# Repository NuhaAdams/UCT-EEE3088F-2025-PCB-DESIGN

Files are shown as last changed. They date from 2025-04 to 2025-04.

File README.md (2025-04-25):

# UCT-EEE3088F-2025-PCB-DESIGN
EEE3088F-MicroMouse Power Subsystem-Group55
# Overall Project
This repository contains the design files, documentation, and supporting resources for the Power Subsystem of the EEE3088F Micro-Mouse course project.
The project involved designing a power board for a micro-mouse maze-solving robot, while the sensing board, processor and motherboard were given.
# The Power Board
The power subsystem is responsible for:
Bidirectional control of 4 motors via H-Bridge drivers (DRV8833PWR).
5V and 3.3V regulated outputs using MC33063AD and TPS62200DBV regulators respectively.
Battery monitoring via INA219 current sensor on the I2C bus.
Battery charging from a USB-C 9V input, with two selectable charging modes (200mA and ~600mA).
High-side switching for two external 5V loads.
System ON/OFF control ensuring <30µA in the OFF state.
The PCB design meets strict budget and dimension constraints, fully interfacing with the Micro-Mouse motherboard.
# How this GitHub repo works
This GitHub repository serves as a central hub for all files related to the power subsystem design of the EEE3088F micro-mouse project.
Each folder in the repository is organized by function. Each of these folders contain the relevant documents that are associated with the design of the power subsystem.

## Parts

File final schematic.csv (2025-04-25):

Reference | Qty | Value | Footprint | LCSC
C1,C6 | 2 | 2.2u | Capacitor_SMD:C_0603_1608Metric_Pad1.08x0.95mm_HandSolder | C12530
C2,C4 | 2 | 0.01u | Capacitor_SMD:C_0805_2012Metric_Pad1.18x1.45mm_HandSolder | C1710
C3,C5 | 2 | 10u | Capacitor_SMD:C_1206_3216Metric_Pad1.33x1.80mm_HandSolder | C7171,C7171
C7,C20,C21 | 3 | 4.7u | Capacitor_SMD:C_0603_1608Metric_Pad1.08x0.95mm_HandSolder | C19666
C8 | 1 | 30p | Capacitor_SMD:C_0603_1608Metric_Pad1.08x0.95mm_HandSolder | C1658
C9 | 1 | 220p | Capacitor_SMD:C_0805_2012Metric | C107145
C10,C14,C16 | 3 | 10u | Capacitor_SMD:C_1210_3225Metric_Pad1.33x2.70mm_HandSolder | C13585,C13585
C11 | 1 | 100u | Capacitor_SMD:C_1210_3225Metric_Pad1.33x2.70mm_HandSolder | C15008
C12 | 1 | 1n | Capacitor_SMD:C_0805_2012Metric | C46653
C13 | 1 | 330u | Capacitor_SMD:CP_Elec_6.3x7.7 | C58277
C15,C17 | 2 | 150u | Capacitor_SMD:CP_Elec_8x10.5 | C38513
C22 | 1 | 0.47u | Capacitor_SMD:C_0603_1608Metric_Pad1.08x0.95mm_HandSolder | C1623
C23,C24 | 2 | 1u | Capacitor_SMD:C_0402_1005Metric_Pad0.74x0.62mm_HandSolder | C52923
C25 | 1 | 4.7u | Capacitor_SMD:C_0504_1310Metric_Pad0.83x1.28mm_HandSolder | C19666
D1 | 1 | 1N5819 | Diode_SMD:D_SMA | C2481
D2,D5 | 2 | LED | LED_SMD:LED_0603_1608Metric | C2286
D6,D7 | 2 | ~ | Diode_SMD:D_SMA-SMB_Universal_Handsoldering | C2481
J1 | 1 | Conn_02x16_Odd_Even | Connector_PinHeader_2.54mm:PinHeader_2x16_P2.54mm_Vertical
J3 | 1 | Conn_01x02 | Connector_JST:JST_PH_S2B-PH-K_1x02_P2.00mm_Horizontal
L1 | 1 | 10u | Inductor_SMD:L_0805_2012Metric_Pad1.15x1.40mm_HandSolder | C1046
L2 | 1 | 100u | Resistor_THT:R_Axial_DIN0411_L9.9mm_D3.6mm_P7.62mm_Vertical | C2931837
Q1 | 1 | 2N7002 | Package_TO_SOT_SMD:SOT-23 | C8545
R1 | 1 | 1 | Resistor_SMD:R_2010_5025Metric_Pad1.40x2.65mm_HandSolder | C2075154
R2 | 1 | 0.4 | Resistor_SMD:R_2010_5025Metric_Pad1.40x2.65mm_HandSolder | C912792
R3,R4 | 2 | 1.8k | Resistor_SMD:R_0603_1608Metric | C4177,C4177
R5 | 1 | 12k | Resistor_SMD:R_0805_2012Metric_Pad1.20x1.40mm_HandSolder | C22790
R6 | 1 | 0.1 | Resistor_SMD:R_2512_6332Metric_Pad1.40x3.35mm_HandSolder | C25334
R7 | 1 | 6k | Resistor_SMD:R_0805_2012Metric_Pad1.20x1.40mm_HandSolder | C2828725
R8 | 1 | 180 | Resistor_SMD:R_0805_2012Metric_Pad1.20x1.40mm_HandSolder | C22828
R9,R13,TH1 | 3 | 10k | Resistor_SMD:R_0603_1608Metric | C25804,C43113
R10 | 1 | 10k | Resistor_SMD:R_0805_2012Metric_Pad1.20x1.40mm_HandSolder | C25804
R11 | 1 | 30k | Resistor_SMD:R_0805_2012Metric_Pad1.20x1.40mm_HandSolder | C2907025
R12,R14 | 2 | 25k | Resistor_SMD:R_0603_1608Metric | C2828637
R16 | 1 | 6.8K | Resistor_SMD:R_0603_1608Metric_Pad0.98x0.95mm_HandSolder | C23212
R17 | 1 | 1.18K | Resistor_SMD:R_0805_2012Metric_Pad1.20x1.40mm_HandSolder | C17374
R18 | 1 | 1M | Resistor_SMD:R_0603_1608Metric_Pad0.98x0.95mm_HandSolder | C22935
R25,R26 | 2 | 1.13K | Resistor_SMD:R_1210_3225Metric_Pad1.30x2.65mm_HandSolder | C5204018
R27 | 1 | 1.5k | Resistor_SMD:R_1210_3225Metric_Pad1.30x2.65mm_HandSolder | C4310
R28 | 1 | 2.9k | Resistor_SMD:R_0805_2012Metric_Pad1.20x1.40mm_HandSolder | C4211
Rsc1 | 1 | 0.2 | Resistor_SMD:R_2512_6332Metric | C459674
TP1,TP2,TP3,TP4,TP5,TP6,TP7,TP8,TP9,TP10,TP11 | 11 | TestPoint | TestPoint:TestPoint_Pad_D2.0mm
U1,U2 | 2 | DRV8833PW | Package_SO:TSSOP-16_4.4x5mm_P0.65mm | C50506
U3 | 1 | INA219AxD | Package_SO:SOIC-8_3.9x4.9mm_P1.27mm | C87469
U4,U6 | 2 | TPS2553DBVR | PCBLIB_SOT-23-6_L2.9-W1.6-P0.95-LS2.8-BR_2025-03-28:SOT-23-6_L2.9-W1.6-P0.95-LS2.8-BR | C55266
U5 | 1 | TPS62200DBV | Package_TO_SOT_SMD:SOT-23-5 | C9048
U8 | 1 | MC33063AD | Package_SO:SOIC-8_3.9x4.9mm_P1.27mm | C127837
U9 | 1 | HX SS12D10G6 | PCBLIB_SW-TH_3P-P4.80-HX-SS12D10G4_2025-03-27 (1):SW-TH_3P-P4.80-HX-SS12D10G4 | C19189121
U10 | 1 | CH224K | Package_SO:SSOP-10-1EP_3.9x4.9mm_P1mm_EP2.1x3.3mm
U11 | 1 | BQ24075RGT | Package_DFN_QFN:VQFN-16-1EP_3x3mm_P0.5mm_EP1.6x1.6mm | C15464
USB1 | 1 | TYPE-C 6P LCH10.0 | PCBLIB_USB-TH_TYPE-C-6P-LCH10.0_2025-03-28:USB-TH_TYPE-C-6P-LCH10.0 | C5187470

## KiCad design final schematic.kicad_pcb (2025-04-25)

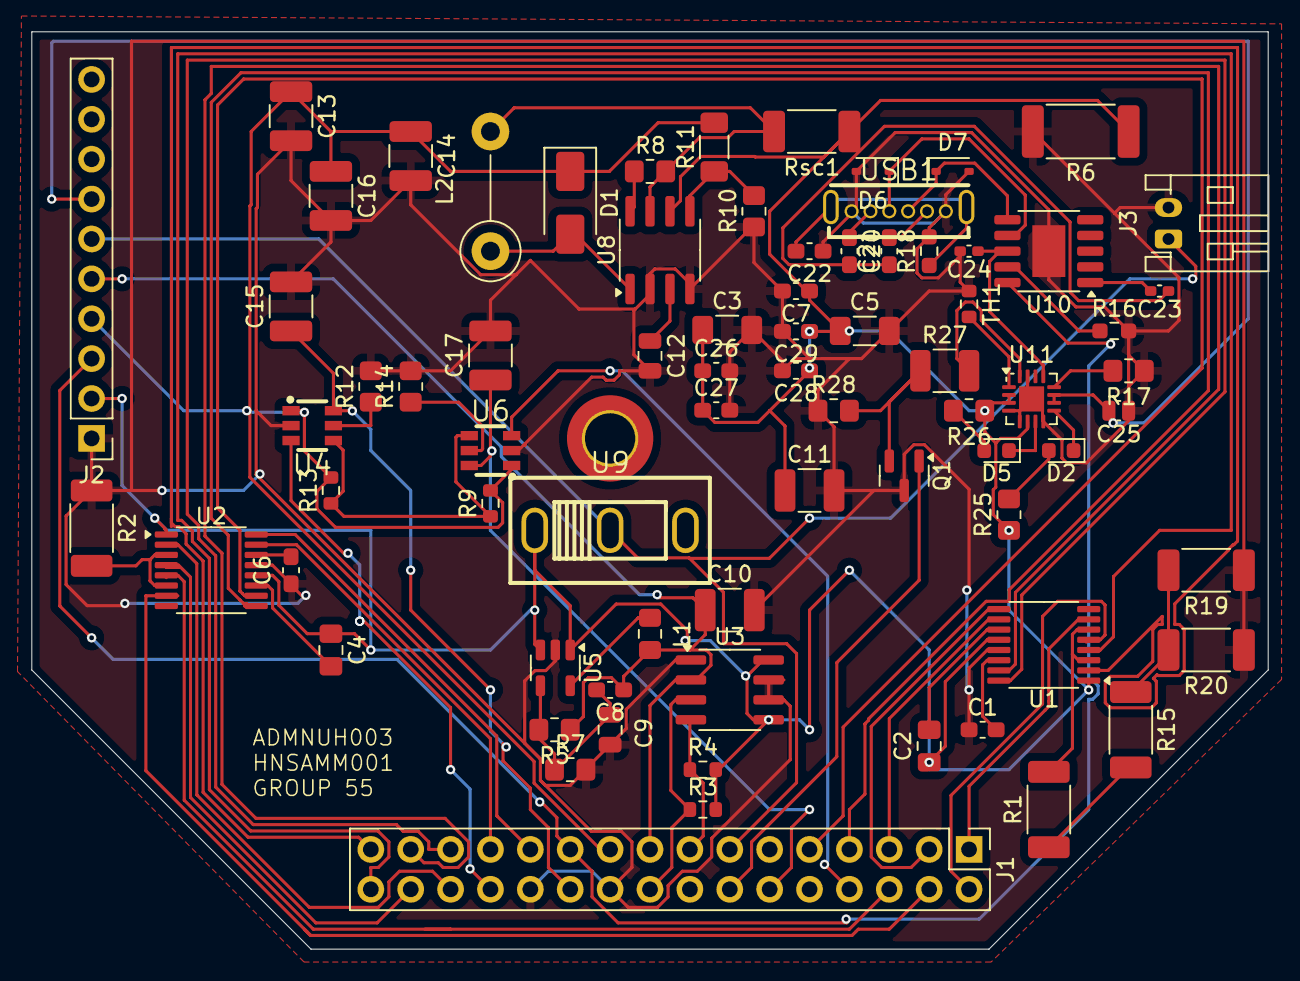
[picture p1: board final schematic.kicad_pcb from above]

Board: 2 copper layers, 78.7 x 58.4 mm, 75 parts (0 on the bottom side), 65 nets.

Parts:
C1, C6: 2.2u; C_0603_1608Metric_Pad1.08x0.95mm_HandSolder
C2, C4: 0.01u; C_0805_2012Metric_Pad1.18x1.45mm_HandSolder
C3, C5: 10u; C_1206_3216Metric_Pad1.33x1.80mm_HandSolder
C7, C20, C21, C26, C27, C28, C29: 4.7u; C_0603_1608Metric_Pad1.08x0.95mm_HandSolder
C8: 30p; C_0603_1608Metric_Pad1.08x0.95mm_HandSolder
C9: 220p; C_0805_2012Metric
C10, C14, C16: 10u; C_1210_3225Metric_Pad1.33x2.70mm_HandSolder
C11, C13, C15, C17: 100u; C_1210_3225Metric_Pad1.33x2.70mm_HandSolder
C12: 1n; C_0805_2012Metric
C22: 0.47u; C_0603_1608Metric_Pad1.08x0.95mm_HandSolder
C23, C24: 1u; C_0402_1005Metric_Pad0.74x0.62mm_HandSolder
C25: 4.7u; C_0504_1310Metric_Pad0.83x1.28mm_HandSolder
D1: 1N5819; D_SMA
D2, D5: LED; LED_0603_1608Metric
D6, D7: D_SOD-323
J1: Conn_02x16_Odd_Even; PinHeader_2x16_P2.54mm_Vertical
J2: Conn_01x10_Pin; PinHeader_1x10_P2.54mm_Vertical
J3: Conn_01x02; JST_PH_S2B-PH-K_1x02_P2.00mm_Horizontal
L1: 10u; L_0805_2012Metric_Pad1.15x1.40mm_HandSolder
L2: 100u; R_Axial_DIN0411_L9.9mm_D3.6mm_P7.62mm_Vertical
Q1: 2N7002; SOT-23
R1, R2, R15, R19, R20: 0.4; R_2010_5025Metric_Pad1.40x2.65mm_HandSolder
R3, R4: 1.8k; R_0603_1608Metric
R5: 56k; R_0805_2012Metric_Pad1.20x1.40mm_HandSolder
R6: 0.1; R_2512_6332Metric_Pad1.40x3.35mm_HandSolder
R7, R10: 10k; R_0805_2012Metric_Pad1.20x1.40mm_HandSolder
R8: 200; R_0805_2012Metric_Pad1.20x1.40mm_HandSolder
R9, R13: 10k; R_0603_1608Metric
R11: 30k; R_1206_3216Metric_Pad1.30x1.75mm_HandSolder
R12, R14: 24k; R_0805_2012Metric_Pad1.20x1.40mm_HandSolder
R16: 6.8K; R_0603_1608Metric_Pad0.98x0.95mm_HandSolder
R17, R26: 1.2K; R_0805_2012Metric_Pad1.20x1.40mm_HandSolder
R18: 1M; R_0603_1608Metric_Pad0.98x0.95mm_HandSolder
R25: 1.2k; R_0805_2012Metric_Pad1.20x1.40mm_HandSolder
R27: 1.5k; R_1210_3225Metric_Pad1.30x2.65mm_HandSolder
R28: 2.9k; R_0805_2012Metric_Pad1.20x1.40mm_HandSolder
Rsc1: 0.4; R_2010_5025Metric_Pad1.40x2.65mm_HandSolder
TH1: 10k; R_0603_1608Metric
U1, U2: DRV8833PW; TSSOP-16_4.4x5mm_P0.65mm
U3: INA219AxD; SOIC-8_3.9x4.9mm_P1.27mm
U4, U6: TPS2553DBVR; SOT-23-6_L2.9-W1.6-P0.95-LS2.8-BR
U5: TPS62200DBV; SOT-23-5
U8: MC33063AD; SOIC-8_3.9x4.9mm_P1.27mm
U9: HX SS12D10G6; SW-TH_3P-P4.80-HX-SS12D10G4
U10: CH224K; SSOP-10-1EP_3.9x4.9mm_P1mm_EP2.1x3.3mm
U11: BQ24075RGT; VQFN-16-1EP_3x3mm_P0.5mm_EP1.6x1.6mm
USB1: TYPE-C 6P LCH10.0; USB-TH_TYPE-C-6P-LCH10.0

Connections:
3V3 Out: C8.1, C10.1, J1.17, J2.5, L1.2, R5.1, U3.2 (A0)
5V Out: C13.1, C14.1, C16.1, D1.1 (K), J1.19, J2.4, R9.2, R11.2, R13.2, U4.1 (IN), U6.1 (IN)
BATTERY: J1.13, J2.6, J3.1, U9.2
CC1: D6.1 (K), U10.7 (CC1), USB1.A5 (CC1)
CC2: D7.1 (K), U10.6 (CC2), USB1.B5 (CC2)
CTRL_EXT_LOAD1: J1.26, U4.3 (EN)
CTRL_EXT_LOAD2: J1.8, U6.3 (EN)
ChargerOut: C25.2, J2.7, U11.10 (OUT), U11.11 (OUT)
EXT_LOAD1_OUT: C15.1, J1.22, U4.6 (OUT)
EXT_LOAD2_OUT: C17.1, J1.12, U6.6 (OUT)
FAST_CHARGE_CTRL: J1.14, Q1.1 (G)
FAULT_SIGNAL_1: R9.1, R13.1, U4.4 (~FAULT), U6.4 (~FAULT)
GND: C1.1, C3.2, C5.2, C6.1, C7.2, C9.2, C10.2, C11.2, C12.2, C13.2, C14.2, C15.2, C16.2, C17.2, C22.1, C24.2, C25.1, C26.2, C27.2, C28.2, C29.2, D6.2 (A), D7.2 (A), J1.20, J1.24, J2.1, J3.2, Q1.3 (D), R2.1, R6.2, R7.2, R10.1, R12.2, R14.2, R16.2, R17.1, R18.2, R19.1, R20.1, R28.1, TH1.1, U1.13 (GND), U2.13 (GND), U3.1 (A1), U3.6 (GND), U3.7 (IN-), U4.2 (GND), U5.2 (GND), U6.2 (GND), U8.2 (SwE), U8.4 (GND), U10.11 (GND), U11.4 (~CE), U11.5 (EN2), U11.8 (VSS), U11.15 (SYSOFF), U11.17 (VSS), USB1.A12 (GND), USB1.B12 (GND)
HV: J1.21, J2.3, U10.10 (PG)
I2C1_SCL: J1.15, R4.1, U3.4 (SCL)
I2C1_SDA: J1.18, R3.1, U3.3 (SDA)
MOTOR1_A_OUT: J1.31, U1.2 (AOUT1)
MOTOR1_B_OUT: J1.32, U1.4 (AOUT2)
MOTOR1_CTRL1: J1.27, U1.16 (AIN1)
MOTOR1_CTRL2: J1.29, U1.15 (AIN2)
MOTOR2_CTRL1: J1.3, U1.9 (BIN1)
MOTOR2_CTRL2: J1.5, U1.10 (BIN2)
MOTOR3_A_OUT: J1.28, U2.2 (AOUT1)
MOTOR3_B_OUT: J1.30, U2.4 (AOUT2)
MOTOR3_CTRL1: J1.23, U2.16 (AIN1)
MOTOR3_CTRL2: J1.25, U2.15 (AIN2)
MOTOR4_CTRL1: J1.7, U2.9 (BIN1)
MOTOR4_CTRL2: J1.9, U2.10 (BIN2)
Motor2_A_OUT: J1.1, U1.7 (BOUT1)
Motor2_B_OUT: J1.2, U1.5 (BOUT2)
Motor4_A_OUT: J1.4, U2.7 (BOUT1)
Motor4_B_OUT: J1.6, U2.5 (BOUT2)
unnamed: C20.1, USB1.A9 (VBUS)
unnamed: C21.2, USB1.B9 (VBUS)
unnamed: C22.2, R18.1, USB1.7 (EH), USB1.8 (EH)
unnamed: D1.2 (A), L2.1, U8.1 (SwC)
unnamed: D2.2 (A), R25.2
unnamed: D2.1 (K), U11.9 (~CHG)
unnamed: D5.2 (A), R26.2
unnamed: D5.1 (K), U11.7 (~PGOOD)
unnamed: Q1.2 (S), R27.1, R28.2
unnamed: R1.1, R15.2
unnamed: R15.1, R19.2, R20.2
unnamed: R1.2, U1.3 (AISEN), U1.6 (BISEN)
unnamed: C2.2, U1.11 (VCP)
unnamed: C1.2, U1.14 (VINT)
unnamed: R2.2, U2.3 (AISEN), U2.6 (BISEN)
unnamed: C4.2, U2.11 (VCP)
unnamed: C6.2, U2.14 (VINT)
unnamed: R12.1, U4.5 (ILIM)
unnamed: C8.2, C9.1, R5.2, R7.1, U5.4 (FB)
unnamed: L1.1, U5.5 (SW)
unnamed: R14.1, U6.5 (ILIM)
unnamed: R8.1, U8.8 (DC)
unnamed: L2.2, R8.2, Rsc1.2, U8.7 (Ipk)
unnamed: C12.1, U8.3 (TC)
unnamed: R10.2, R11.1, U8.5 (Vfb)
unnamed: R16.1, U10.9 (CFG1)
unnamed: C23.2, U10.1 (VDD)
unnamed: R17.2, U11.12 (ILIM)
unnamed: R27.2, U11.16 (ISET)
unnamed: TH1.2, U11.1 (TS)
SWITCH_INPUT: C2.1, C3.1, C4.1, C5.1, C7.1, C11.1, C26.1, C27.1, C28.1, C29.1, J2.2, R3.2, R4.2, R6.1, R25.1, R26.1, Rsc1.1, U1.1 (nSLEEP), U1.12 (VM), U2.1 (nSLEEP), U2.12 (VM), U3.5 (VS), U3.8 (IN+), U5.1 (VI), U5.3 (EN), U8.6 (Vin), U9.1, U11.2 (BAT), U11.3 (BAT), U11.6 (EN1)
USB C: C20.2, C21.1, C23.1
V_BUS: C24.1, U10.8 (VBUS), U11.13 (IN)
